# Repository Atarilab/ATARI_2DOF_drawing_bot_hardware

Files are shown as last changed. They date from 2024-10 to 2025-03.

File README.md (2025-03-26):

# ATARI_2DOF_drawing_bot_hardware

GO HERE FOR SOFTWARE: [ATARI_2DOF_Drawing_Bot](https://github.com/Atarilab/ATARI_2DOF_Drawing_Bot)

This repository contains all the necessary information and files to build a ATARI 2DOF drawing robot.
The goal of this build is to have a system solely consisting of off the shelf parts and 3D printed parts while keeping costs down.

## Off the shelf parts

The parts listed here can be purchased from multiple online stores and retailers. If the linked stores provided in this documentation don't have the necessary parts in stock or don't deliver to your country, it shouldn't be a problem to order from a different retailer. In case you are not using the provided links for purchasing the parts, make sure that all specs and dimensions of the components match the ones listed here.

### Electronic parts

| Part | Description | Quantity | Link |
|-|-|-|-|
| Esp32 | Microcontroller running the SimpleFOC algorithm for motor control| 1 | [Link](https://www.conrad.de/de/p/az-delivery-esp32-dev-kit-c-unverloetet-kompatibel-mit-arduino-850037836.html) |
| SimpleFoc Mini v1.0 | Motor control board | 2 | Easiest to find on AliExpress via search for 'SimpleFOC Mini v1.0' |
| BLDC gimbal motor gbm2804h | Brushless DC motors | 2 | Easiest to find on AliExpress or Amazon via search for 'BLDC gimbal motor gbm2804h' |
| AS5600 Magnetic Encoder | Encoder for measuring motor angle | 2 | [Link](https://funduinoshop.com/elektronische-module/sensoren/bewegung-distanz/magnetinduktives-winkelmess-sensormodul-as5600) |
| Power supply, 12V, 3A | Power supply | 1 | [Link](https://www.conrad.de/de/p/mean-well-gst36e12-p1j-steckernetzteil-festspannung-12-v-dc-3000-ma-36-w-1439200.html) |
| DC power socket 5.5x2.1mm | Power supply socket | 1 | [Link](https://www.conrad.de/de/p/tru-components-niedervolt-steckverbinder-buchse-einbau-vertikal-5-5-mm-2-1-mm-1-st-1582319.html) |
| Micro USB cable | For ESP32 connection | 1 | - |

### Mechanical parts

| Part | Description | Quantity | Link |
|-|-|-|-|
| Ball bearing 17x26x5mm | - | 3 | - |
| Ball bearning 5x11x5mm | - | 2 | - |
| Screw M3x6mm flat head | - | 28 | - |
| Screw M3x10mm flat head | - | 8 | - |
| Screw M2x4mm round head | - | 12 | - |
| Screw M2x16mm flat head | - | 4 | - |

### Tools

| Tool | Comment | Link |
|-|-|-|
| Screwdrivers | According to which screws are being used | - |
| Dupont crimp tool | For crimping cables to custom lengths | [Link](https://www.berrybase.de/crimpzange-fuer-dupont-steckverbinder-an-kabel-awg-18-28) |
| Soldering iron | For soldering wires to DC power socket | - |
| 3D printer | For printing all structural parts | - |
| Pliers wrench | Not essential, but helpful for pressing in ball bearings | [Link](https://www.hoffmann-group.com/DE/de/hom/p/813702-180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) |
| Countersink hand tool | Not essential, but useful for cleaning up countersunk holes of 3D printed parts | [Link](https://www.hoffmann-group.com/DE/de/hom/p/150400-12%2C4?tId=509&wayIntoCart=SRP&triggerSelectItemEvent=1) |
| Utility knife | not essential, but practical for cleaning up sharp edges of 3D printed parts | [Link](https://www.hoffmann-group.com/DE/de/hom/p/844800-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) |

### Cables

Ideally the cables for this build are crimped to guarantee good contacts and durability. Alternatively, the cables can also be soldered if being done with caution.
Use this dupont crimp tool or a similar crimp tool with the corresponding dupont crimps so your cables will be compatbile with the rest of th electronics.
| Part | Link |
|-|-|
| Dupont crimp tool | [Link](https://www.berrybase.de/crimpzange-fuer-dupont-steckverbinder-an-kabel-awg-18-28) |
| Dupont crimps | [Link](https://www.berrybase.de/en/610-teiliges-dupont-crimp-steckverbinder-set-in-kunststoffbox) |

#### Power cable

#### Magnetic encoder cable

#### Motor cable

## 3D printed parts

| Part | Description | Quantity |
| - | - | - |
| Housing | Housing for all electronics components | 1 |
| Housing lid | Lid of the housing | 1 |
| Magnet pouch | Plate that holds the magnet for the AS5600 magnetic encoder | 2 |
| Shaft socket | Socket for connecting the shaft of the input gear to the motor | 2 |
| Input gear | Smaller gear of the transmission | 2 |
| Output gear | Bigger gear of the transmission | 2 |
| Rear Arm (L11 / L12) | - | 2 |
| Front arm L (L21) | - | 1 |
| Front arm R (L22) | - | 1 |
| Pen holder | Pen holder for a standard Stabilo pen; The model might neeed adjustment for other pens | 1 |

## Assembly

### Preparing components

- Clean up all rough edges and holes of the 3D printed components
- Solder 90-degree angled pin headers onto AS5600 PCB
- Solder straight pin headers onto ESP32 (Ideally only the pins that are necessary)
- Cut wires to the correct lengths and crimp dupont connectors onto their ends
- Solder wires onto the DC power socket (2x12V and 2xGND) and crimp dupont connectors onto the loose ends
- Cut motor cables to correct length and crimp dupont connectors onto the loose ends (3 pins)
- Screw M2x16 screw into the hollow shaft of the input gear

### Assembly of the housing
1. Mount the ESP32 board into the housing by using the mounting holes in the center of the housing. The Micro USB connector should be accessible from outside the housing.
2. Mount the two SimpleFOC Mini into the housing by using the outermost mounting holes
3. Connect the SimpleFOC data connectors (cables with 5 pins) to the SimpleFOC Minis and to the ESP32
4. Connect 3.3V supply cables to AS5600s
5. Connect I2C cables (2 pins) to the AS5600s and to the ESP32
6. Mount AS5600s into the housing by using the mounting holes next to the SimpleFOC Minis
7. Connect the 3.3V supply cables of the AS5600 magnetic encoders to the SimpleFOC Minis
8. Mount the DC power socket into the housing by using the large mounting hole in the wall next to the ESP32
9. Connect the cables of the DC power socket to the SimpleFOC Minis supply pins

### Assembly of the drive train
1. Mount motors onto the bottom side of the housing lid by using the inner mounting holes
2. Push the shaft of the input gear through the hollow motor shaft. Stick the shaft socket onto the end of the shaft of the input gear and insert a M2x16mm into the hole on the side of the shaft socket.
3. Insert the round magnet of the AS5600 magentic encoder into the magnet pouch
4. Align the holes of the magnet pouch and of the shaft socket with the mounting holes on the motor and screw four M3x10mm screws into the holes.
5. Press large ball bearings into the recesses on the bottom sides of the output gears
6. Press the output gears onto the round protrusions on the top side of the housing lid
7. Press small ball bearings into the holes on the ends of the rear arms
8. Press plastic pins at the ends of the front arms into the ball bearings on the rear arms
9. Press a big ball bearing into the hole on the end of the left front arm
10. Press the end of the right front arm into the big ball bearing of the left front arm
11. Mount the two links onto the output gears using M3x6mm screws
12. Connect the motor cables to the SimpleFOC Minis
13. Mount the assembled housing lid onto the housing using M3x6mm screws

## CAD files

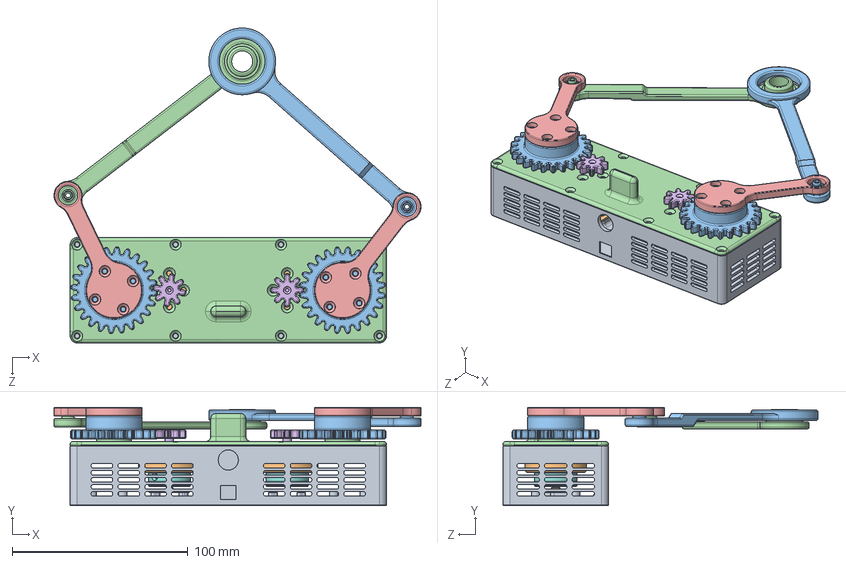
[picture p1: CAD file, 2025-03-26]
CAD/Solidworks/drawing_bot_assembly.SLDASM
208.8 x 56.0 x 179.2 mm
housing_lid
output_gear x 2
GBM2804H-100T x 2
housing
shaft_socket x 2
magnet_pouch x 2
input_gear x 2
rear_arm x 2
front_arm_L
front_arm_R
As5600_module
magnet

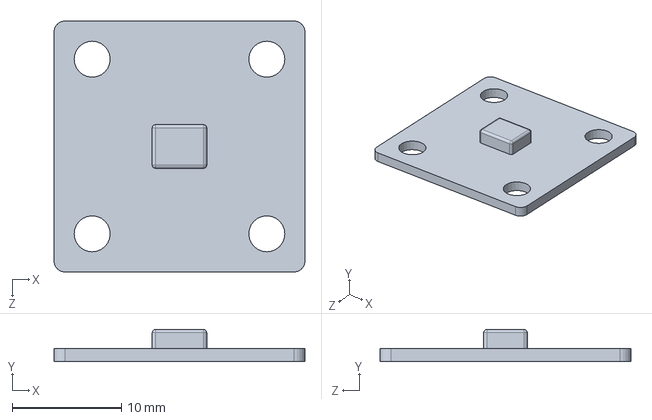
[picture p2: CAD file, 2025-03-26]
CAD/Solidworks/helper/As5600_module.SLDPRT
23.0 x 2.95 x 23.0 mm

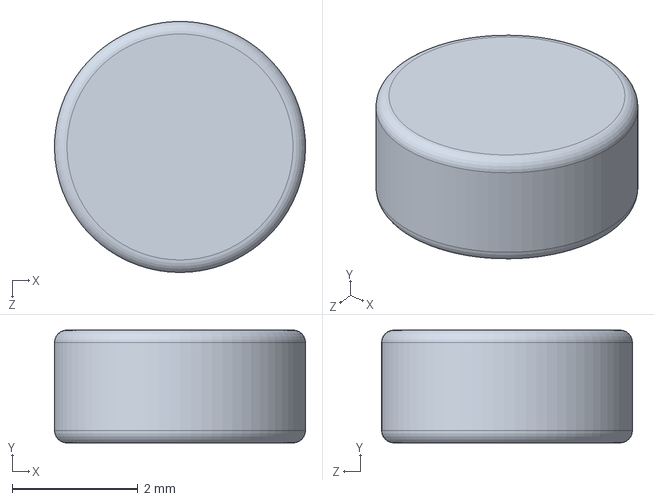
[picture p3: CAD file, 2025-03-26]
CAD/Solidworks/helper/magnet.SLDPRT
4.00 x 1.80 x 4.00 mm

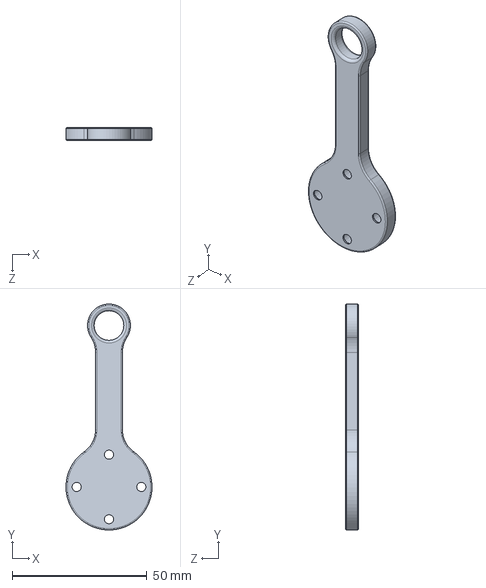
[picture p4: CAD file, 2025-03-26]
CAD/Solidworks/rear_arm.SLDPRT
32.0 x 84.0 x 5.00 mm

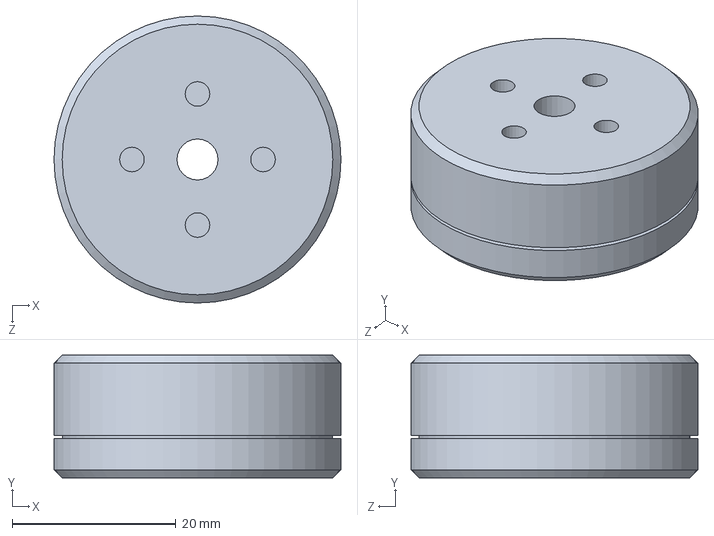
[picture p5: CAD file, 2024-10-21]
CAD/Solidworks/helper/GBM2804H-100T.SLDPRT
35.0 x 15.0 x 35.0 mm

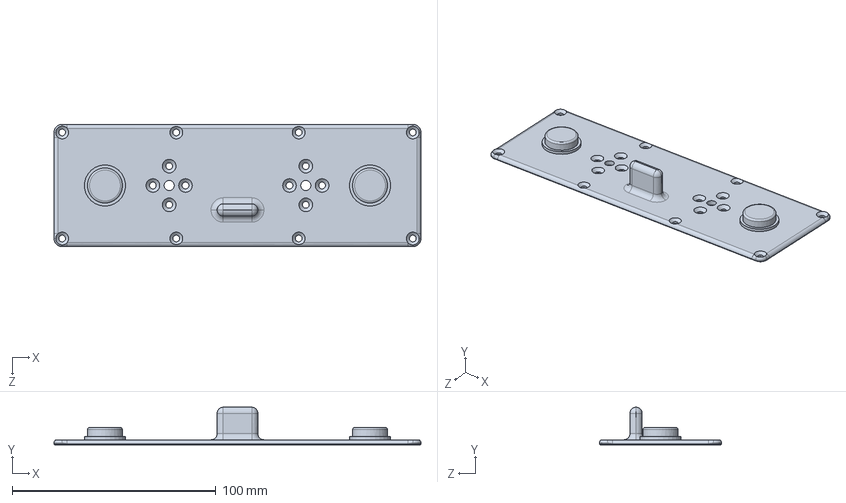
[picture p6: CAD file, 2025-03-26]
CAD/Solidworks/housing_lid.SLDPRT
180.0 x 18.5 x 60.0 mm

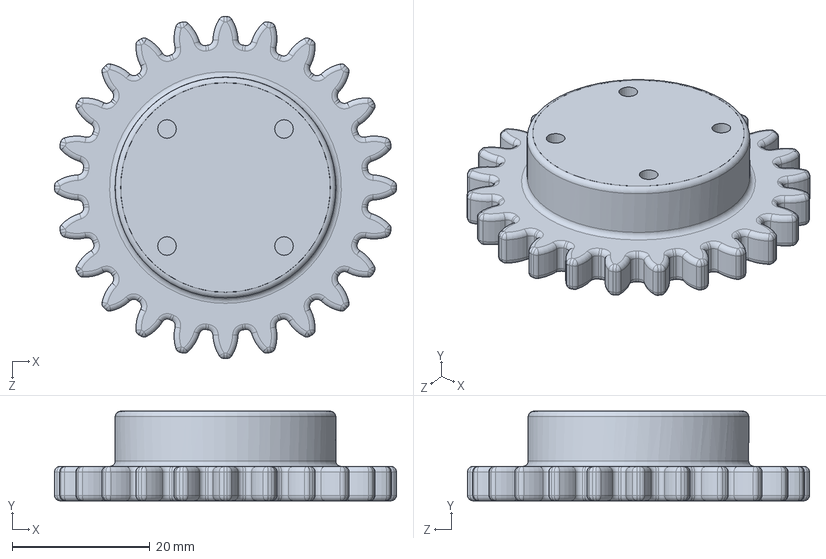
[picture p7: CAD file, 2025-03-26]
CAD/Solidworks/output_gear.SLDPRT
49.6 x 13.0 x 49.6 mm

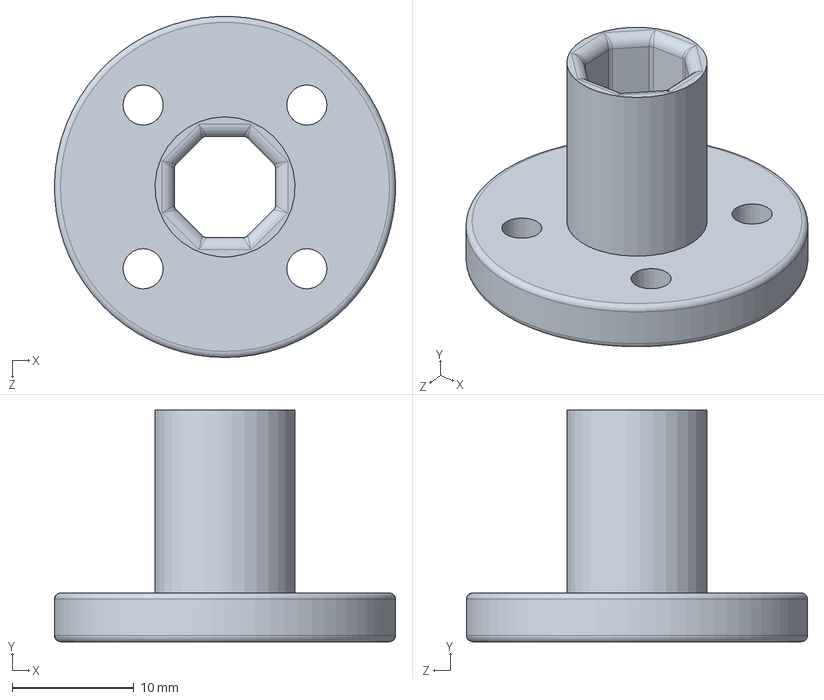
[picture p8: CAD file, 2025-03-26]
CAD/Solidworks/pen_holder.SLDPRT
28.0 x 19.0 x 28.0 mm

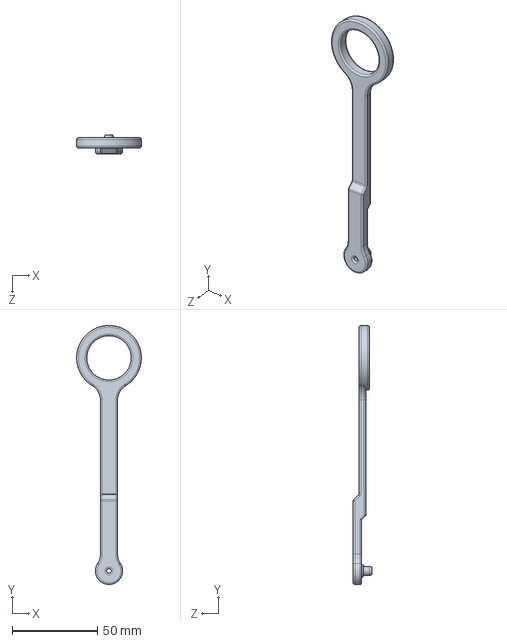
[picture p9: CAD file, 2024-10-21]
CAD/Solidworks/front_arm_R.SLDPRT
38.0 x 152.0 x 11.0 mm

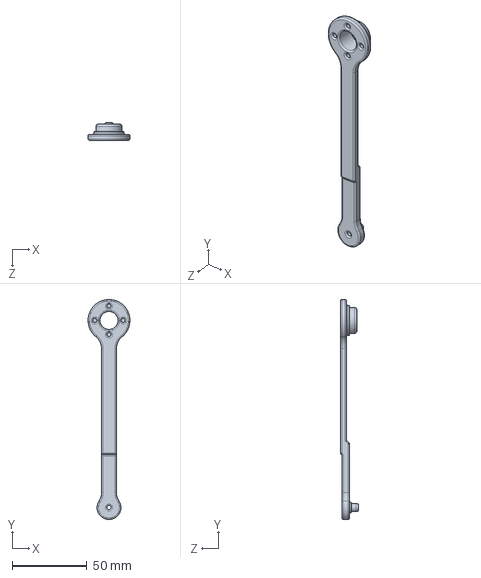
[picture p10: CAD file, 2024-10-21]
CAD/Solidworks/front_arm_L.SLDPRT
28.0 x 147.0 x 12.0 mm

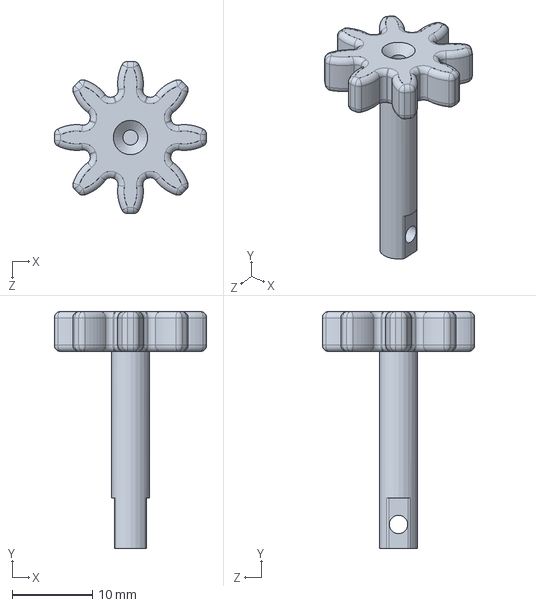
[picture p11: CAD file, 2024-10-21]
CAD/Solidworks/input_gear.SLDPRT
19.0 x 29.6 x 19.0 mm

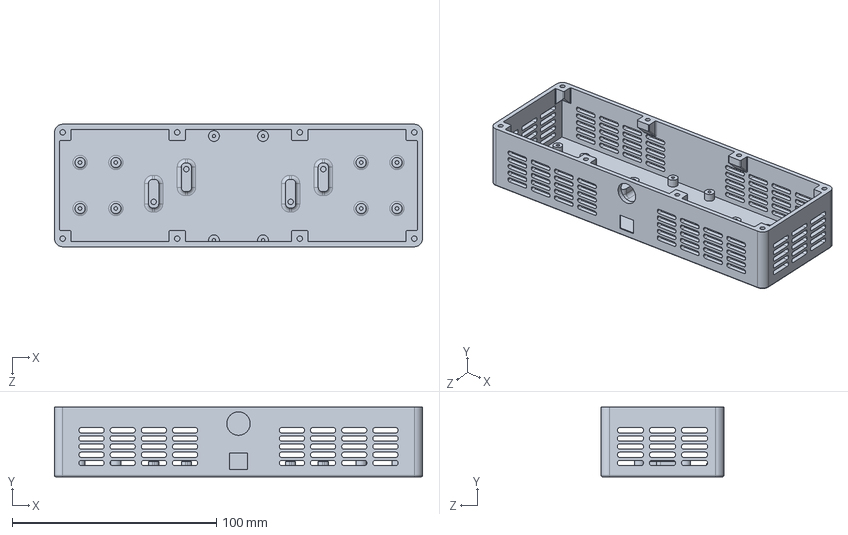
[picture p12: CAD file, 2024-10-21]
CAD/Solidworks/housing.SLDPRT
180.0 x 34.0 x 60.0 mm

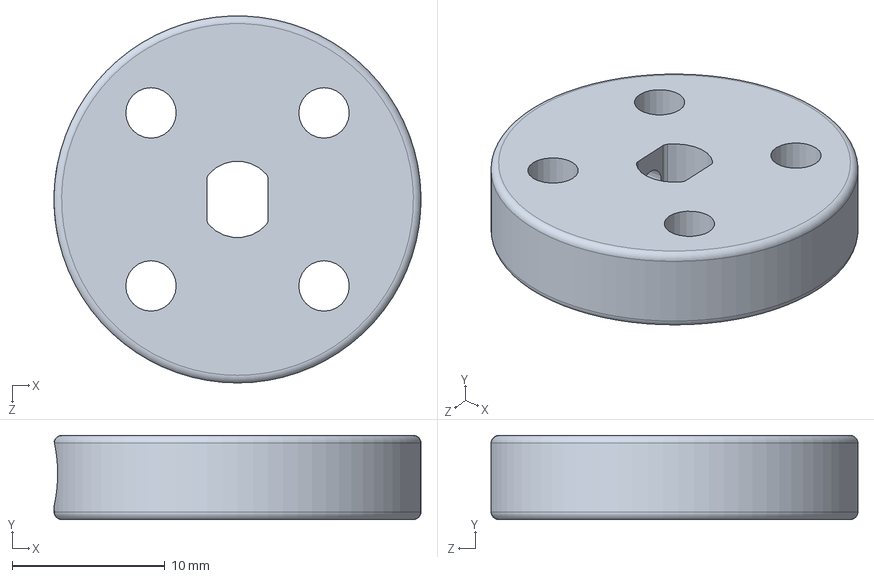
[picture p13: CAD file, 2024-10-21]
CAD/Solidworks/shaft_socket.SLDPRT
24.0 x 5.50 x 24.0 mm

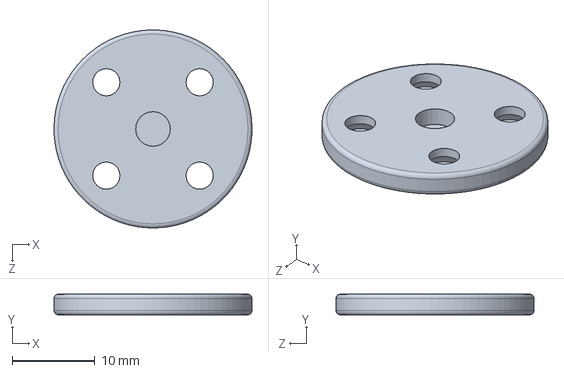
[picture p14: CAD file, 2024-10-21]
CAD/Solidworks/magnet_pouch.SLDPRT
24.0 x 2.50 x 24.0 mm

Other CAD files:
CAD/STLs/front_arm_L.STL
CAD/STLs/front_arm_R.STL
CAD/STLs/housing.STL
CAD/STLs/housing_lid.STL
CAD/STLs/input_gear.STL
CAD/STLs/magnet_pouch.STL
CAD/STLs/output_gear.STL
CAD/STLs/pen_holder.STL
CAD/STLs/rear_arm.STL
CAD/STLs/shaft_socket.STL

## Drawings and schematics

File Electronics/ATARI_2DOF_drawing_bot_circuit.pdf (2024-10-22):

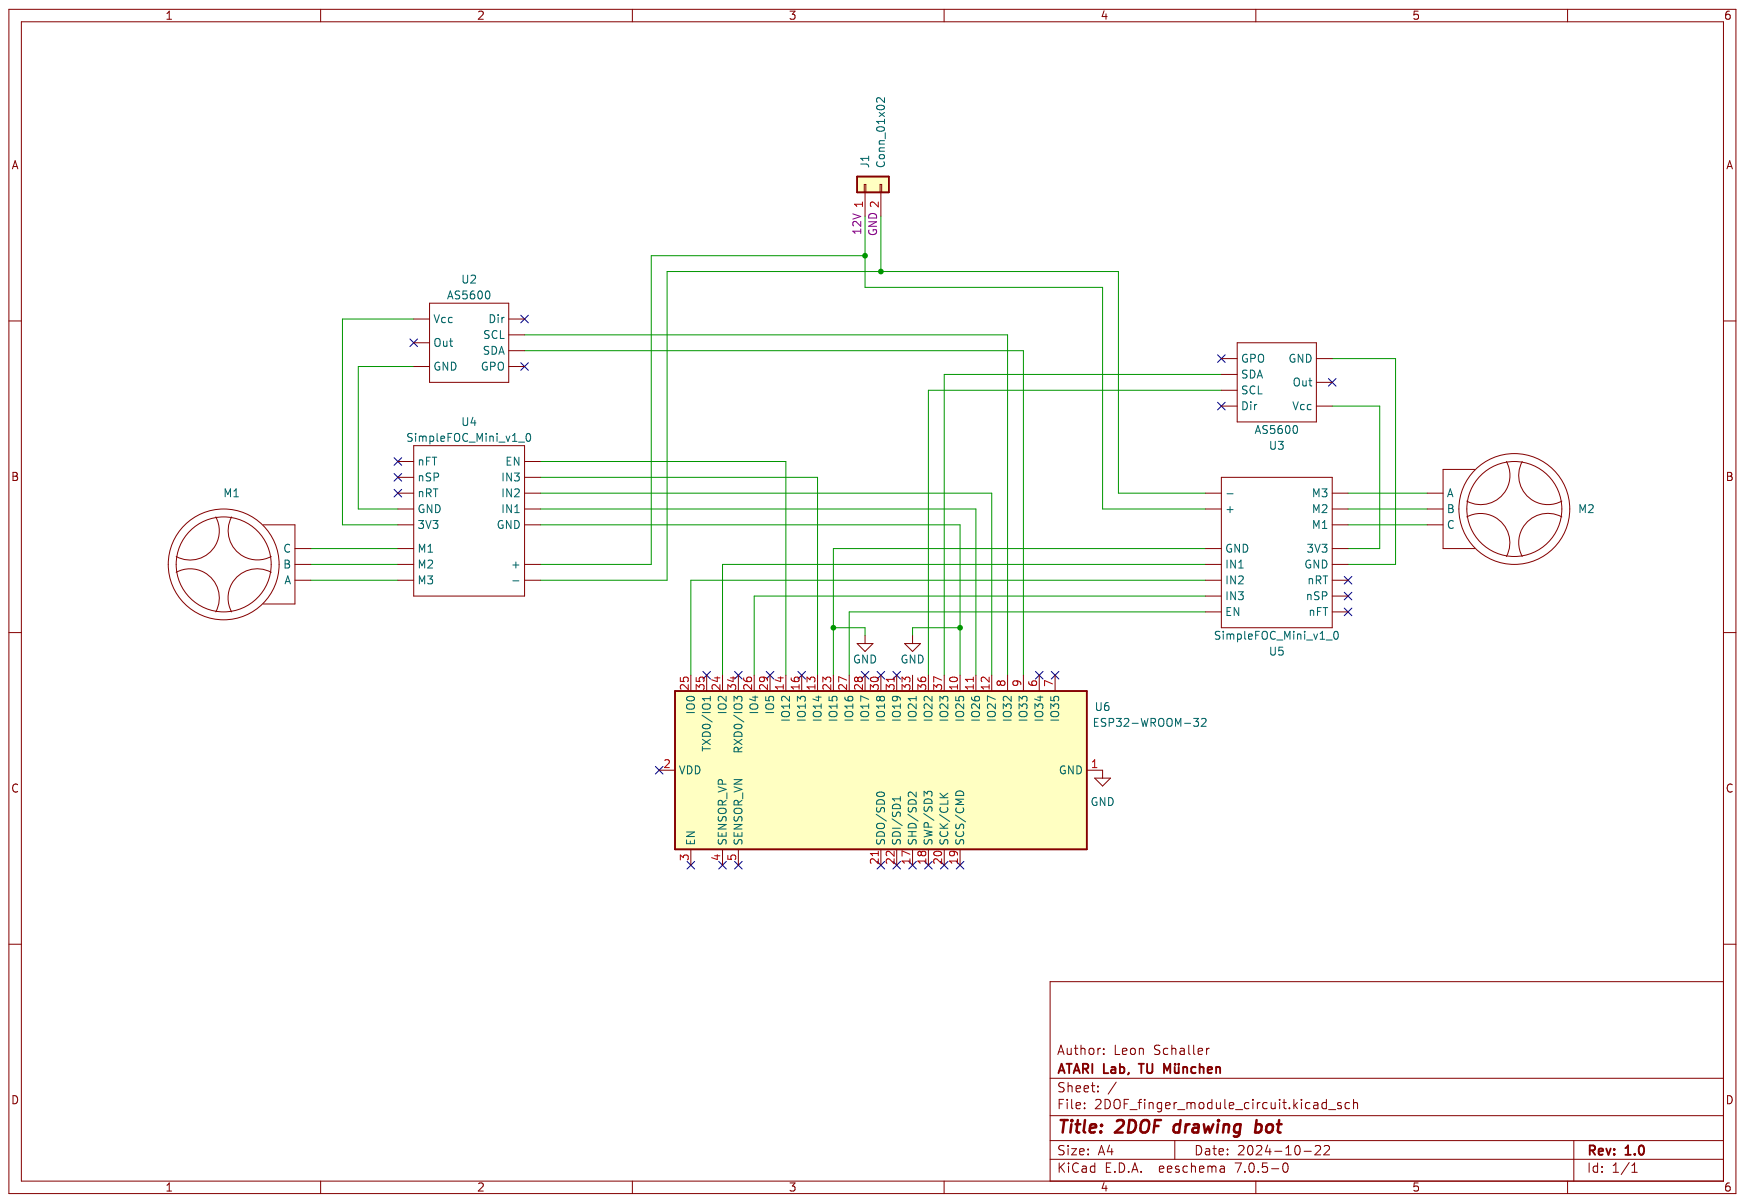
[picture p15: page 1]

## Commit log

2024-10-22 Added electronics documentation
    [2DOF_finger_module_circuit.kicad_pcb, 2DOF_finger_module_circuit.kicad_sch]
2025-03-26 Added CAD files
    [As5600_module.SLDPRT, GBM2804H-100T.SLDPRT, drawing_bot_assembly.SLDASM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]
